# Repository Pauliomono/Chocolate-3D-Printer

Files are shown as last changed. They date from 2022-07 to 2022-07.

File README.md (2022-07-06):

# Chocolate-3D-Printer

3D printer that prints edible chocolate!
 
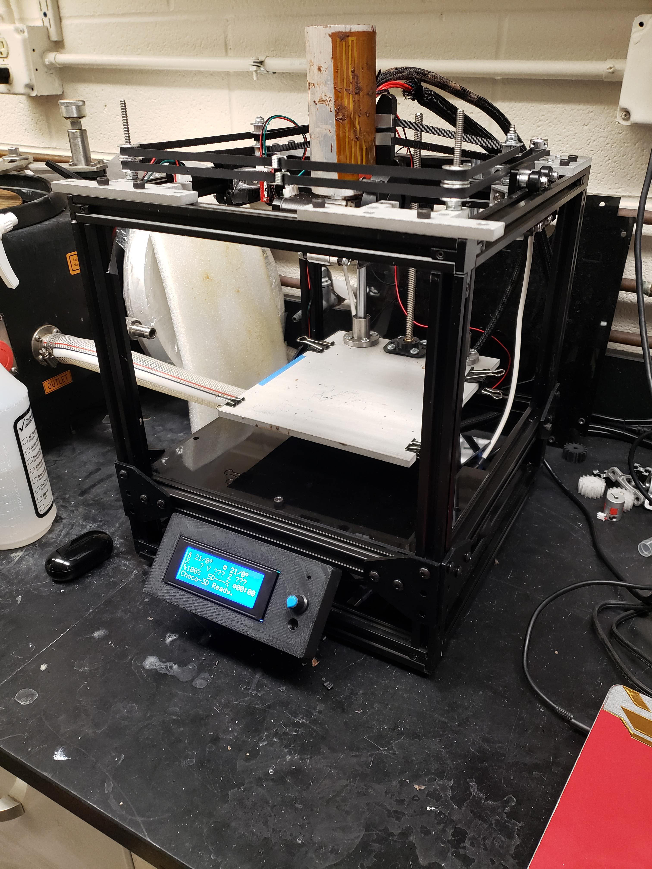
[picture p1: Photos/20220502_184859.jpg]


This 3D printer is capable of printing 3D objects from standard 3D printer .gcode files, such as the 3D Benchy demonstration print shown below.

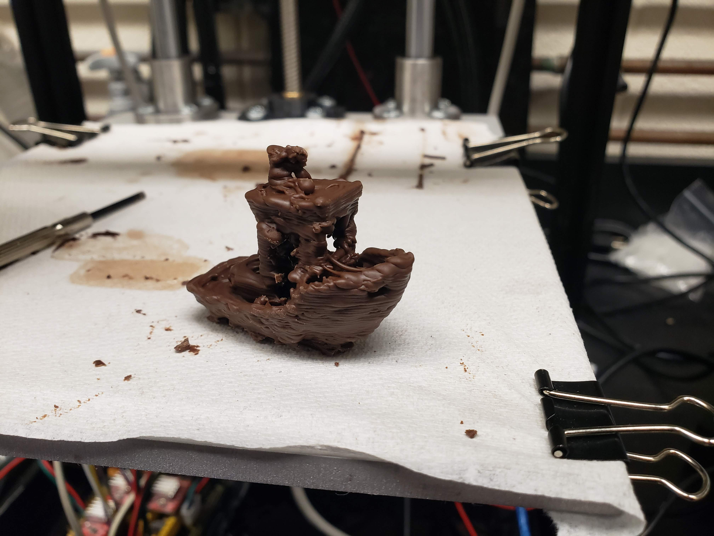
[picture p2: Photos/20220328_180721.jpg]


The Chocolate 3D Printer was designed in 2 iterations: the first as a group project during fall 2021 senior design and the second as an independent design project I worked on spring 2022.

For detailed information, the final report on this project is available under "Independent Design Project Final Report.pdf"

This project was created as a Mechanical Engineering Senior Design Project at the University of Notre Dame. Credit to Kassidy, Max, Morgan, and Thomas who were my teammates. The Chocolate 3D Printer is still equally yours as it is mine.

(printer in operation)



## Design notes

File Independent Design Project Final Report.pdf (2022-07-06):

Independent Design Project Spring 2022

Chocolate 3D Printer V2.0

Paul Mellor

May 3, 2022

Part 1: Original Project Overview

This project started as a Senior Design Project in the fall semester of 2021. The project was to

build a chocolate 3D printer (3DCP) that printed chocolate rather than plastic. It had the

following customer requirements: [1]

1. The 3DCP must print custom, detailed patterns and shapes out of chocolate.
2. The product must be safe to eat, durable, and taste good.
3. The 3DCP must create the pattern in a reasonable amount of time.
4. The 3DCP must be easy and safe to use.
5. The 3DCP should not require user intervention during the print.
6. The 3DCP must be easy to clean.
7. The 3DCP can be handled by up to two people and fit on the counter.
8. The 3DCP must be presentable and suitable for display.
9. The 3DCP can produce multiple copies during one print.
10. Power consumption is suitable for a standard household wall outlet.
11. The 3DCP must be affordable.

Based on the requirements we were given for Senior Design, a quantified list of design

specifications were created as the goals we intended to meet for the project. [1]

1. Through a combination of nozzle diameter, a recommended melting temperature of 31-36

°C, motor precision, and motion tolerance, the printer must be able to produce details as

small as 2 mm. The 3DCP nozzle diameter must not exceed 2 mm.

2. All parts of the 3DCP that come in contact with chocolate must be able to be washed and

be nontoxic in the 31-36 °C region. For example, any chocolate in contact with vinyl

tubing must not exceed 79.4 °C.

3. The volumetric flow rate should be at least 25 cm³
/hr.
4. All conductible materials near the heat source will have insulation or a cover and no

material will exceed 60 °C to avoid burns.

5. The 3DCP must store chocolate for the entire print: at least 100 cm³
of chocolate.
6. The parts must be able to come apart and fit together in order to clean easily. To remain

dishwasher safe, all materials must have a melting point above 180 °F.

7. OSHA standards specify that two people can comfortably carry 102 lbs. This 3DCP will

not exceed 51 lbs. The dimensions of the base will not exceed 2ft x 2ft

8. The 3DCP must have a viewing window that is at least 10 cm x 10 cm. All wires, motors

and electronics will be hidden.

9. The 3DCP must have a build area that is at least 10 cm x 10 cm.
10. The 3DCP must not use more than 1500 W of power.
11. The 3DCP fabrication must not exceed $1000 in purchased and manufactured parts.

These specifications drove the design choices we made for the original 3DCP.

Initial Design

The CAD model for the original design is shown below in Figure 1.

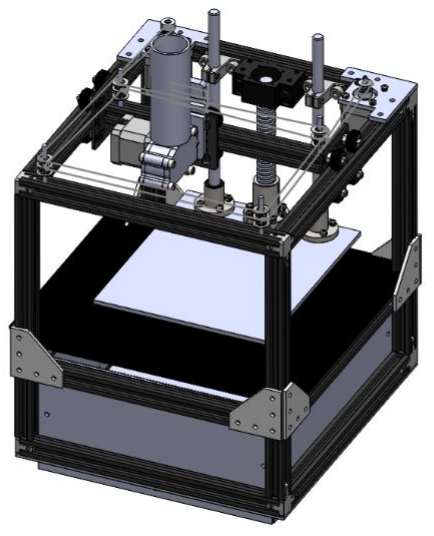
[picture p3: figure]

Figure 1: CAD model of the original 3DCP

To get a system that moved in 3 dimensions, the motion system moved the extruder in the x-y

plane while the build plate moved in the z direction. This was selected in order to minimize the

amount of power needed to quickly move the mass of the extruder body, vat, and chocolate

against the force of gravity. Starting with this principle, a CoreXY motion system was identified

which met the design specifications. Based on a specific arrangement of timing belts, it allows

the extruder to move anywhere in the x-y plane while the motors are fixed in place. A diagram of

this belt arrangement is shown in Figure 2.

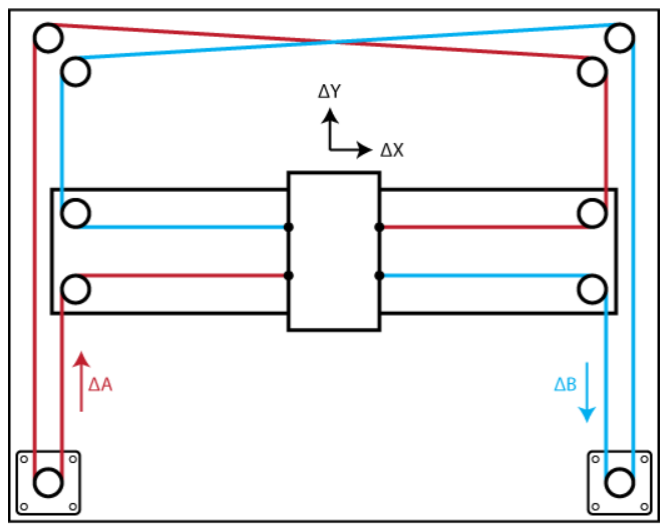
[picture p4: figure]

Figure 2: CoreXY diagram

The build plate was moved in the z direction using a combination of a lead screw and linear

guide rails. The gear reduction provided by the lead screw meant that a powerful motor wasn’t

necessary to hold the build plate against gravity. The guide rails kept the build plate stable and

took the bending loads of the bed.

The extruder design was modelled on a commercially available design called the

ChocoL3D extruder [2]. This was a gear-pump based design as opposed to the more common

syringe design. The gear pump extruder was chosen initially in order to minimize space taken by

a large syringe body and to improve the aesthetics of the design. It also allows better control for stopping and starting the extruder. Several iterations of the extruder were prototyped and tested

before the design was finalized and fabricated. The extruder design is shown below in Figure 3.

Electronics

The original design used an Arduino Mega as the microcontroller for the printer. It used a

“RAMPS 1.4 3D Printer Shield” that allowed it to interface with motors, heaters, and sensors.

The motors selected were stepper motors. They were simple to use with Arduino code, easy to

position with a high degree of precision, compatible with the RAMPS Shield, and powerful

enough to move the CoreXY motion system. 12V Electric heating elements were selected to heat

the gear pump and the vat for the extruder. Each also had a corresponding thermistor to provide

temperature feedback to the Arduino. A wiring diagram is shown in Figure 3.

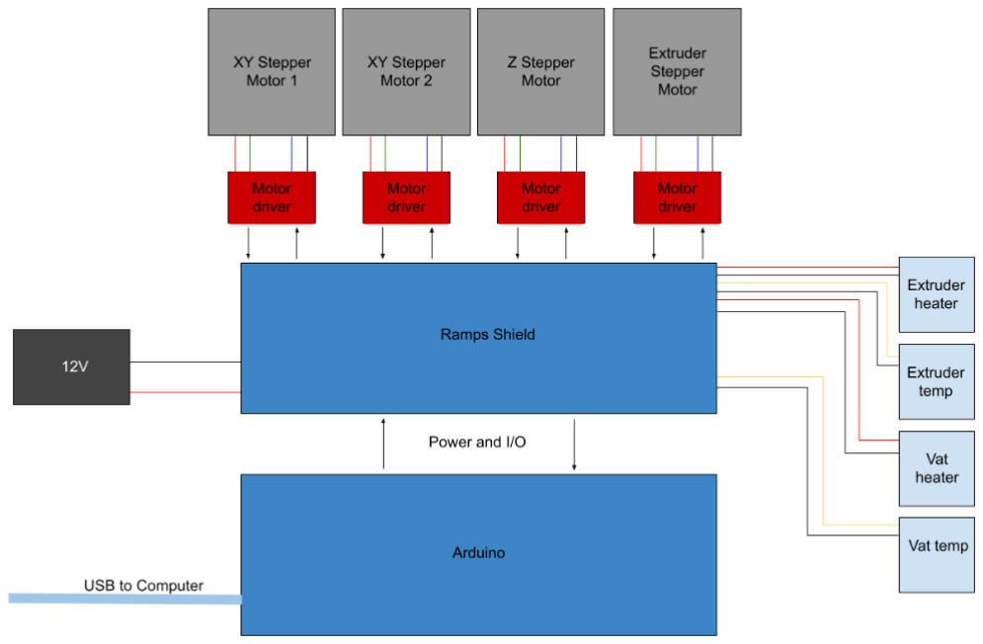
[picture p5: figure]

Figure 3: Wiring diagram of the Arduino

Software

In the original software system 3DCP began with a stereolithography (.STL) file for the

desired print object. The .STL file was imported into Cura, where it gets sliced and a G-Code file generated. The G-code file was converted into a .txt file and imported into MATLAB. A

MATLAB program parsed through the .txt file to interpret the G-Code and convert it to the

necessary coordinates to position the motors. The MATLAB program identified redundant layers

from the slicer to optimize storage space on the Arduino. The program outputted three matrices

of data points. The first two are the X and Y coordinates of the extruder. The third is a matrix full

of ones and zeros indicating if the extruder should be extruding during a given pass between

points.

These matrices were copied and pasted into the Arduino code and uploaded to the

Arduino board. The Arduino code then iterated through the matrices and performed the

necessary calculations for CoreXY to move the extruder carriage via two stepper motors. A third

stepper motor lowered the base plate between layers of chocolate. Once the Arduino code was

compiled, the board is connected to power to start the print. Figure 4 is a flowchart outlining the

sequence of the original software.

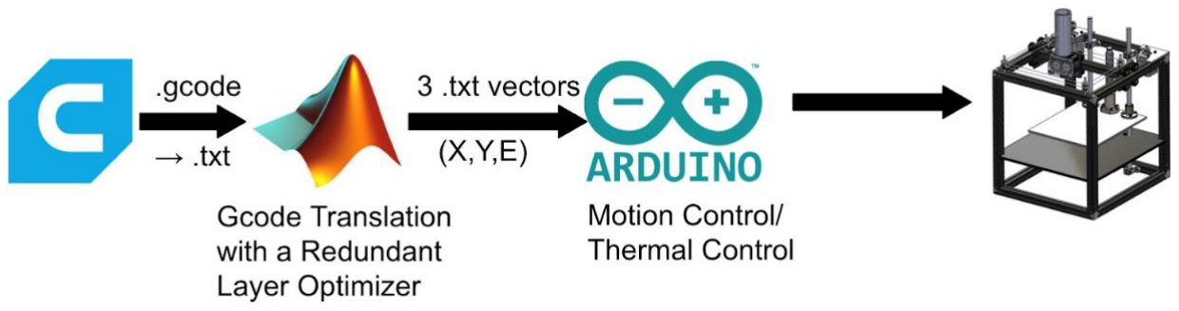
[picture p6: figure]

Figure 4: Flowchart of the Software System.

Results at the End of Senior Design

Figure 5 shows the 3DCP at the conclusion of Senior Design.

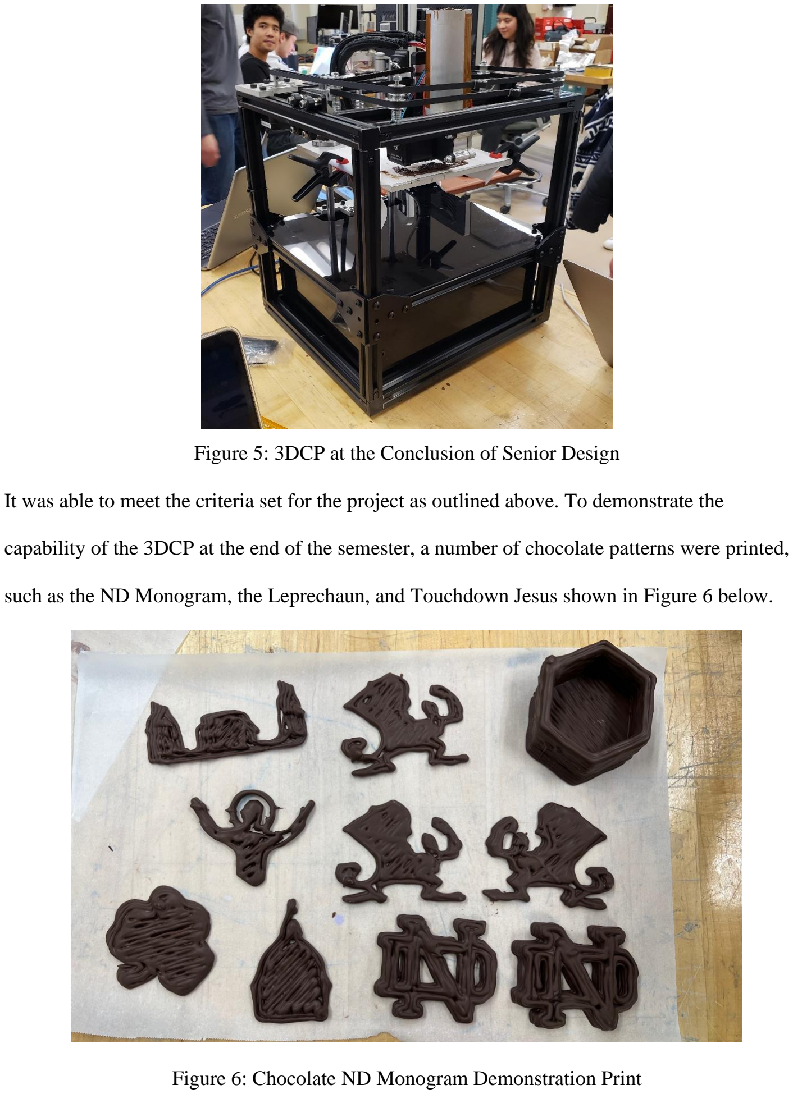
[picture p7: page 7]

Figure 5: 3DCP at the Conclusion of Senior Design

It was able to meet the criteria set for the project as outlined above. To demonstrate the

capability of the 3DCP at the end of the semester, a number of chocolate patterns were printed,

such as the ND Monogram, the Leprechaun, and Touchdown Jesus shown in Figure 6 below.

Figure 6: Chocolate ND Monogram Demonstration Print

Additionally, the 3DCP was capable of larger 3D prints, like the chocolate vase also pictured

above in Figure 6.

Problems

While this senior design project was successful, it was a good first iteration with

significant room for improvement. There were a number of issues that limited the printer’s

capability, and made it difficult to use. The first issue was the workflow required to go from 3D

model to completed 3D print. Using MATLAB to process the G-Code was confusing and

unintuitive. Reprogramming the Arduino for every new print was also a step that anyone without

programming experience would have a hard time completing, and made the 3DCP a rather

unadaptable system. This also had an unintended consequence – by making the coordinates for

the 3D print part of the code, the size of the print file was limited to the amount of flash memory

on the Arduino. In practice, this meant that any of our 3D prints had to contain less than ~800

distinct coordinates, severely limiting the complexity of geometry the 3DCP could print. This

effectively limited the 3DCP to printing a “thick 2D print” (printing the same pattern for every

layer).

- requirement of computer
- workflow to go from 3D model to actually printing
- limit to 2D shapes
- wait time between layers

Another problem with the 3DCP is that the chocolate took several minutes to solidify. This

meant that 1 layer could be printed reasonably quickly, but then the printer would have to wait

several minutes between layers before printing the next layer. The result was print times that

were sometimes double or triple in length to the time the printer spent actually moving.

- reliability (extruder working inconsistently, broken ball screw)

The last major problem the 3DCP had was reliability problems. First, extruder performance was

inconsistent. Sometimes it would produce consistent flow of chocolate, sometimes it would only

extrude chocolate in bursts, and sometimes it wouldn’t extrude any chocolate. Part of this had to

do with a finicky pre-heating procedure which involved reprogramming the Arduino with

separate code just to get everything up to temperature and flowing.

Part 2: The Second Iteration to Create Printer 2.0

With the foundation of the 3DCP from Senior Design, new goals were set to create a second

iteration of the 3DCP. These new additional goals were:

1. The 3DCP is able to print true 3D files. This includes more difficult structures like

overhangs and bridges.

2. The 3DCP can manage the heat of the printed chocolate such that it does not have to stop

printing in order for it to cool.

3. The 3DCP is user friendly enough that it can be operated by an average person who isn’t

necessarily experienced with 3D printing.

Software Changes

For the second iteration of the 3DCP the software was completely overhauled. The

Arduino was programmed with an open source piece of code called “Marlin”. Marlin is a

customizable piece of firmware specifically written for 3D printers. It is used on many

commercial 3D printers. It has a built-in G-code interpreter and can print directly using a G-code

file. It handles all of the kinematics of the motor, with built-in configurations for CoreXY motion

systems. It handles the heaters using sophisticated PID controllers. It has built-in functionality for adding a user interface. Finally, it designed to use an SD card (or some external storage

media) for storing G-code files.

Switching to Marlin has significant advantages over the original code written for the

3DCP. First, it greatly simplified the workflow going from a 3D file to a printed 3D object.

Instead of slicing in Cura, parsing in MATLAB, and reprogramming the Arduino, the sliced file

straight from Cura only needs to be placed on an SD card and connected to the controller.

Someone with little to none programming experience can translate a 3D file into something the

3DCP can print with Marlin. Second, the use of an SD card effectively removes the limitation on

the number of coordinates for the 3D print. Even highly detailed 3D models don’t come close to

the gigabytes level capacities of an SD card. Finally, if G-code files are left on the SD card, the

3DCP can be operated without any access to a computer whatsoever.

Cooling System

For the second iteration of the 3DCP, a cooling system was added to the printer. To

decrease the time needed to print, the extruded chocolate needed to solidify as quickly as

possible. Two approaches were considered to solve this issue: either cool the chocolate using

conduction through the build plate, or cool the chocolate using forced convection from a fan.

Conduction was ultimately decided against. While chilling the build plate would likely be very

effective at cooling the first few printed layers, the more layers that were built up, the less

effective conductive cooling would be. Since convection could provide consistent cooling

performance regardless of the number of layers in the print, a study was done to see if forced

convection from a fan could effectively cool the chocolate more quickly.

To find the feasibility of using convective cooling to help solidify the chocolate, a

cooling calculation was done to simulate how effectively convection could cool a layer of chocolate. A 20mm x 20mm x 1.5mm box was used to represent the shape of a single chocolate

layer. Using the lumped capacitance method, the temperature T of the chocolate as a function of

time is given by:

T(t) = T∞ + (T0 − T∞)e

−

t
τ

where T∞ is the ambient temperature, T0 is the initial temperature, and τ is the time constant. τ is

equal to

τ =

cpρV
ℎA

where cp is specific heat (1006 J/kg-K) [4] , ρ is density (1.225 kg/m^3) [4], V is volume, ℎ is

the convection coefficient, and A is surface area. ℎ for forced convection from a fan was taken to

be a conservative 60 W/m^2-K [4]. A plot comparing the forced convection from a fan to natural

convection is shown in figure 7.

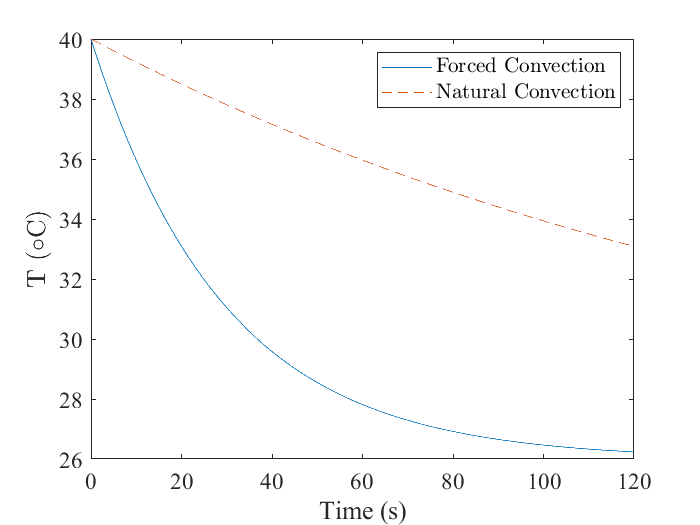
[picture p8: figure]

Figure 7: Theoretical Convective Cooling for Chocolate

This demonstrated that adding a fan would make a significant difference in cooling the

chocolate quickly. Based on Figure 7, cooling the chocolate from the print temperature of 40 ℃

to below to melting point of 32 ℃ only took 25 seconds – significantly less than the 3+ minutes

required between layers at the end of senior design. Based on this proof of concept, a cooling fan

was added to the extruder, shown in figure 8 below.

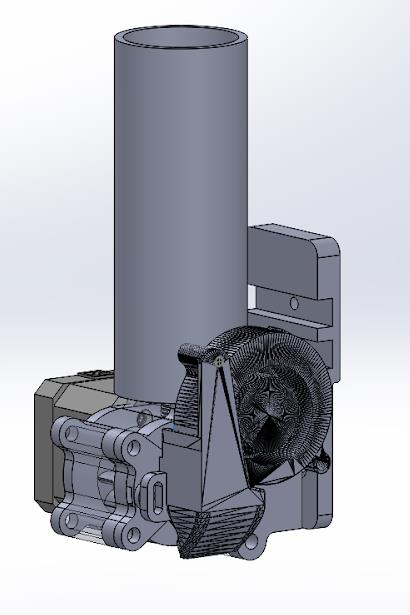
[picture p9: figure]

Figure 8: Cooling System on the Extruder

User Interface

For the second iteration of the 3DCP, a user interface was added. A small display and a

control knob were added to the front of the 3DCP. The screen can be used to show useful

information about the printer, show menus for controlling and configuring the printer, and

initiate 3D prints. The control knob can be used to navigate these menus and select items. In

conjunction with Marlin as the firmware, a whole host of useful functionality is now readily available to anyone using the printer. Examples of the home screen and available menus are

shown in Figures 9 and 10 below.

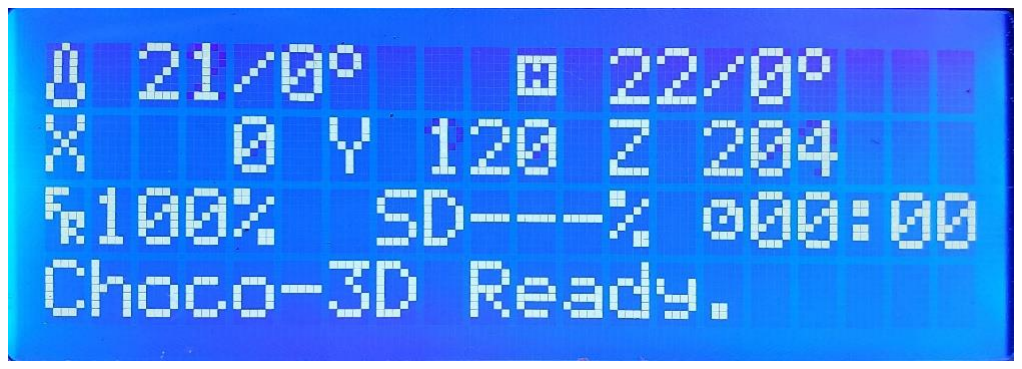
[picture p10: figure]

Figure 9: Home Screen

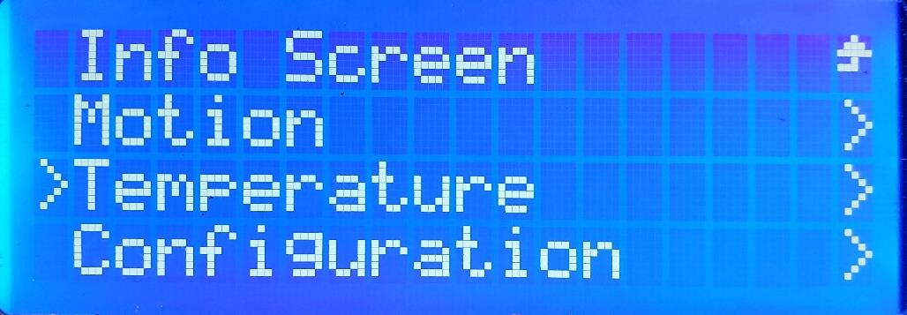
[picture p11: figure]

Figure 10: Menus on the 3D printer

Documentation & Resources

In addition to adding a user interface, a whole host of documentation and resources were

created to make the 3DCP accessible and usable by inexperienced persons. First, the SD card on

the 3D printer is loaded with multiple premade print files. A user can simply plug the printer in,

select one of these files, and the printer automatically starts. No experience with a 3D printer

slicer is required.

If a user wants to print their own 3D model, a slicing profile was created for CURA

Slicer. Uploading this profile automatically changes the slicer parameters (layer thicknesses, line

widths, flow rates, temperatures, retraction settings, supports, etc) to specifically work with the

3DCP. This allows someone without much experience with 3D printing slicers to still print their

own custom 3D models.

Finally, the biggest resource created for the 3DCP was a user guide. This guide gives

step-by-step instructions for turning on and warming up the printer, generating the G-code files

for 3D prints, and starting a 3D print. It also includes a troubleshooting guide to help fix

common issues that might occur with the 3DCP. This document is attached in the Appendix.

Results

Figure 11 shows the 3DCP at the conclusion of the spring semester.

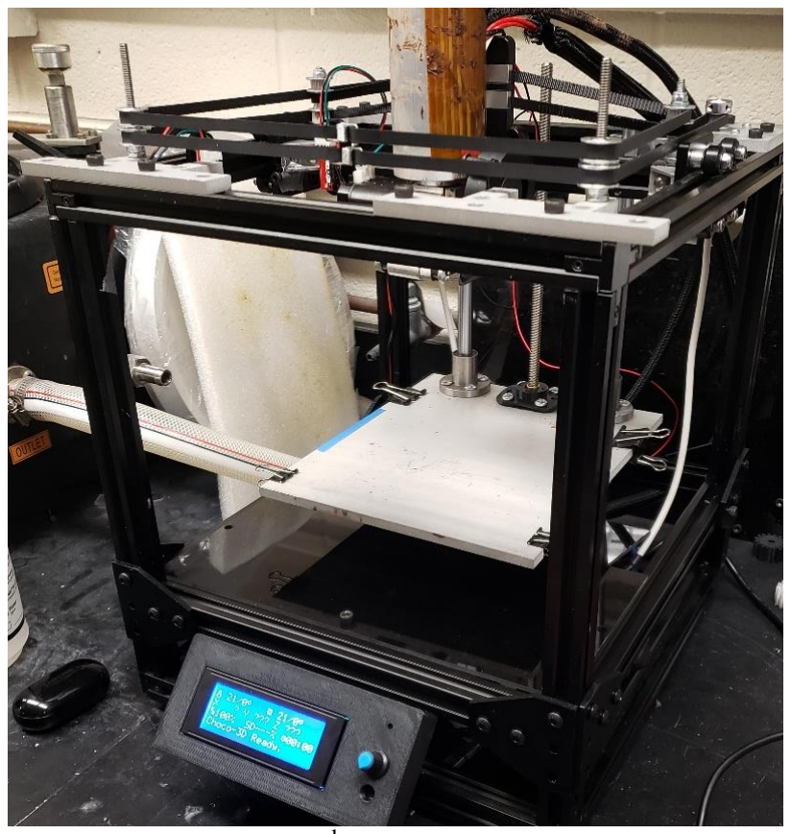
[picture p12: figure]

Figure 11: 2nd Iteration of the 3DCP

Most of the printer remains unchanged from the first iteration, but its capabilities have vastly

improved in terms of printer performance and usability. The 3DCP is now able to print true 3D

models with complex geometry. An example of what it is now capable of printing is shown in

Figure 12.

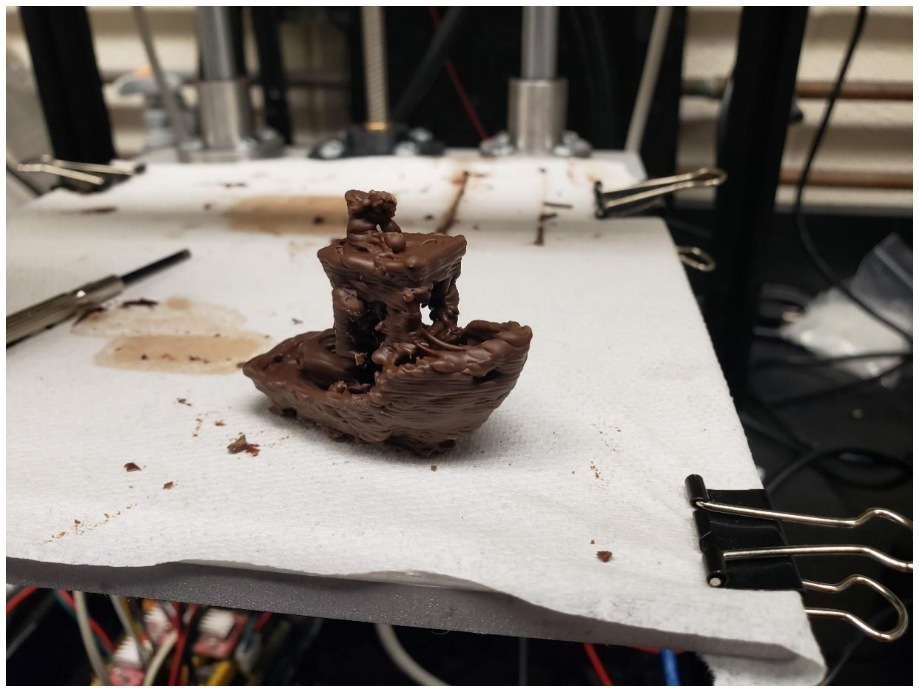
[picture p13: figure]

Figure 12: Example of Chocolate 3D Print Compared to the 3D Model

This print has overhangs, bridges, complex details, and was printed in only 30 minutes. The

finished print is dimensionally within ±1mm of the original 3D model. Finally, the 3DCP was

able to cool the chocolate well enough that it only had to pause between layers for the uppermost

layers of the smokestack that only took a few seconds each to print.

To evaluate the user friendliness of the 3DCP, several people unfamiliar with the 3DCP

were given the user documentation and resources and shown the 3DCP. They were then asked

print the model shown in Figure 12 (The print file was premade and already loaded on the SD

Card in the 3DCP). All of them were able to successfully start the print with the use of the

provided resources. One person was even able to start the 3D print without consulting the

documentation whatsoever, and commented that the menus on the printer were surprisingly

intuitive to follow.

Remaining Areas for Improvement

This second iteration of the 3DCP represented a huge step forward for the 3DCP, but

there are still remaining areas where the 3DCP could improve. First, the 3DCP still only works

with one kind of chocolate. More time could be spent testing with different chocolate types and

tuning the printer to work with different materials. This would make the printer more

flexible/adaptable instead of locking it to exclusively the chocolate it prints with now.

Secondly, the 3DCP does not print with a consistent line width, especially at slow speeds.

This is likely due to the gear pump design for the extruder not producing consistent pressure at

low speeds. A combination of redesigning the geometry of the gear pump and increasing the

print speed could either mitigate this issue or fix it altogether.

Third, the gear pump design does not work well with smaller nozzle sizes. For nozzles

smaller than 1mm in diameter, the extruder tends to jam and does not extrude at all. Redesigning

the gear pump may fix this problem, but this may also be a limitation of the gear pump concept

for the extruder.

Finally, the 3DCP lacks some features that are common “nice to have” features often

found on many normal 3D printers. It does not have a bed levelling mechanism, quiet motors, a

camera to watch/record the printing process, or internet connectivity. While not strictly necessary

to the operation of the 3DCP, these are features that would make the 3DCP a more well rounded

product.

Appendix A: References

[1] Senior Design Design Proposal, Group 5, Notre Dame AME Senior Design Fall 2021
[2] ChocoL3D, L3D Extruder’s Body. https://chocol3d.com/product/l3d-extruder-kit/
[3] Convection Heat Transfer Coefficients, Philip Kosky,

https://www.sciencedirect.com/topics/engineering/convection-heat-transfer-coefficient

[4] Air Specific Heat Capacity, Engineering Toolbox, https://www.engineeringtoolbox.com/air-

specific-heat-capacity-d_705.html (https://www.engineeringtoolbox.com/air-specific-heat-capacity-d_705.html)

Appendix B: User Guide

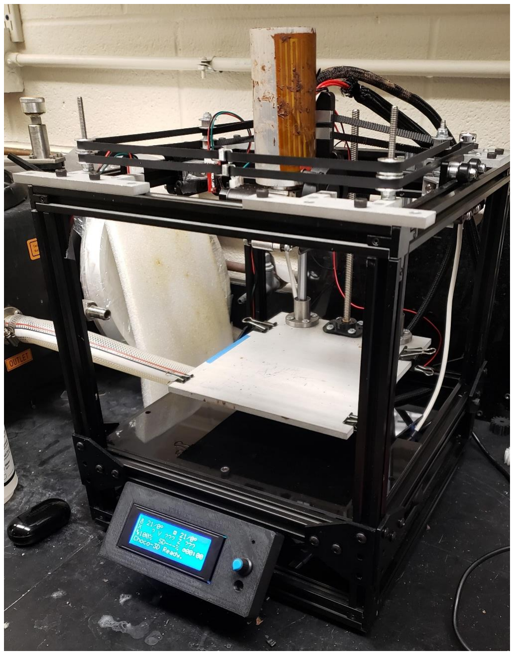
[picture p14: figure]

# The 3D Chocolate Printer

# (3DCP)

# User Guide

Overview

This is the home info screen for the 3DCP.

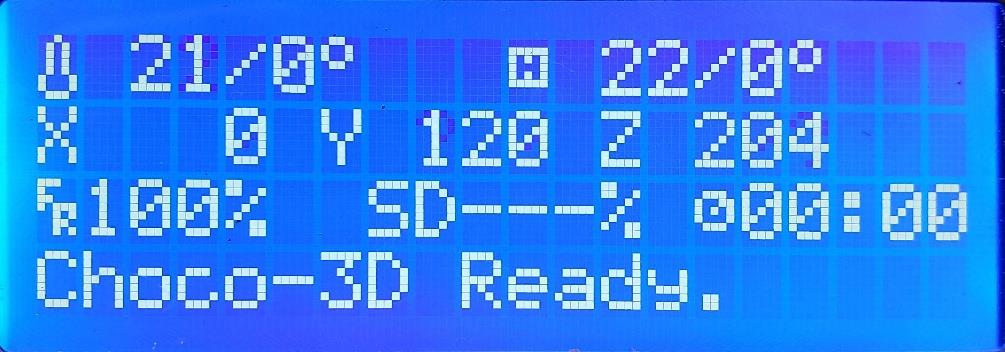
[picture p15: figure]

It gives a host of information about the printer.

- The top row shows the temperature of the of the Chocolate Vat and the Extruder.
- The 2nd row shows the position of the printer in millimeters.
- This may be inaccurate until the printer has been homed (The 3DCP will home itself automatically at the beginning of every print)
- The 3rd row tracks the progress of a 3D print, showing both % completed and time elapsed.
- The bottom row displays any relevant messages or errors the 3DCP might have.

To the right of the screen is the control knob.

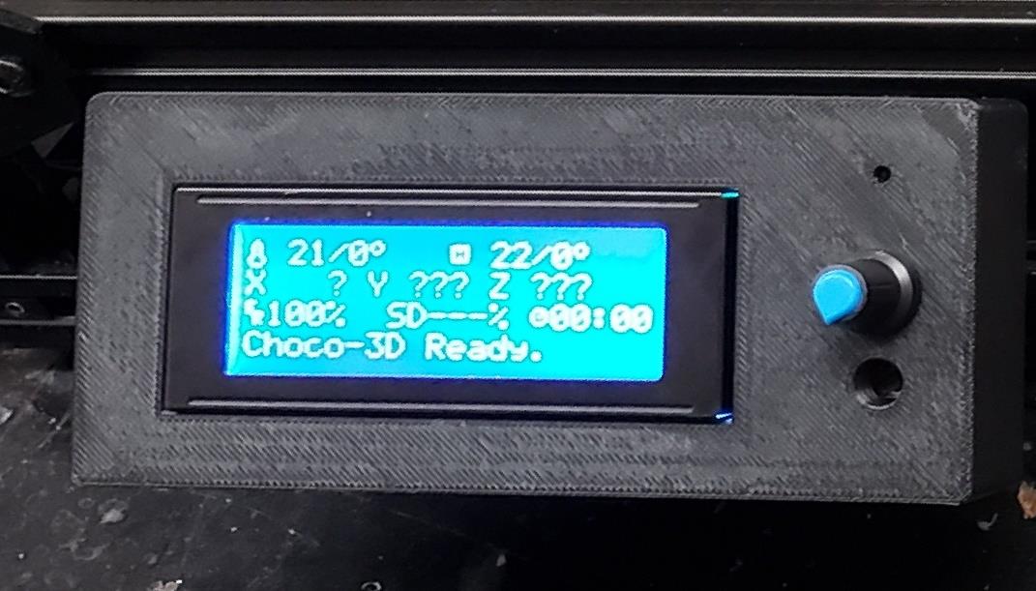
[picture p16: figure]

Twisting this knob allows the user to scroll through menus. Pressing the knob allows the user to select something.

On the left side of the screen is the SD card slot. This is where print files are stored, and this is how print files are moved from a computer to the 3DCP.

Preheating Procedure

Before starting any prints, the 3DCP must be preheated. This procedure melts the chocolate so that it is able to be printed. DO NOT START A PRINT UNTIL THE PREHEATING PROCEDURE IS COMPLETE.

1. To start the preheat, open the main menu and select “Temperature”:
2. Select “Preheat Choco”:

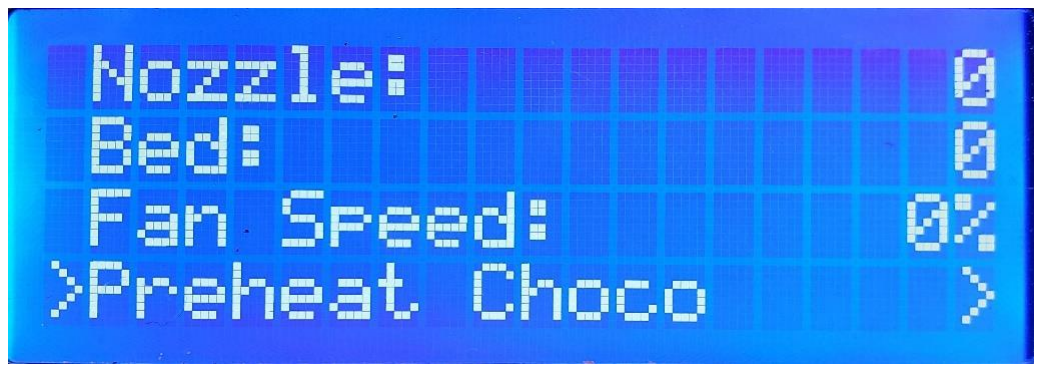
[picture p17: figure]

3. Select “Preheat Choco”:

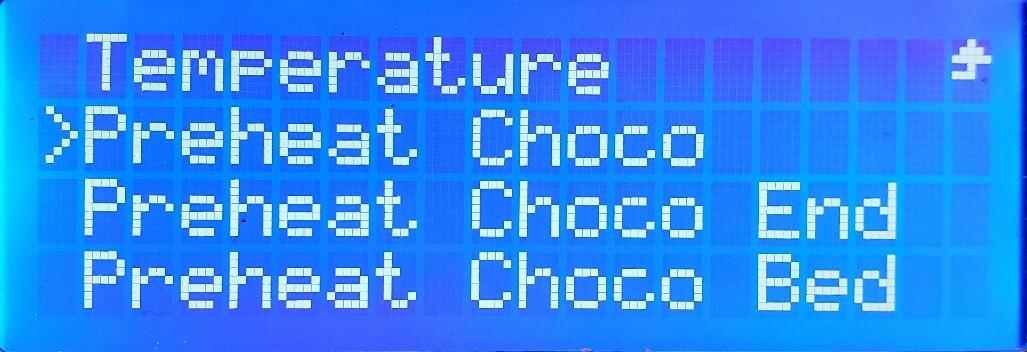
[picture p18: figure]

4. Once this is completed, return to the home screen.
5. WAIT. This step may take 10-15 minutes. Periodically check the chocolate in the vat. When the Chocolate in the vat is melted, the Preheating Procedure is complete. The 3DCP is now ready to print.

Start a 3D Print

Ensure that the preheating procedure has been completed before starting a print. The 3DCP will not print properly until the chocolate is warmed up and melted.

1. To start a 3D print, open the main menu and scroll down to select “Print from Media”:

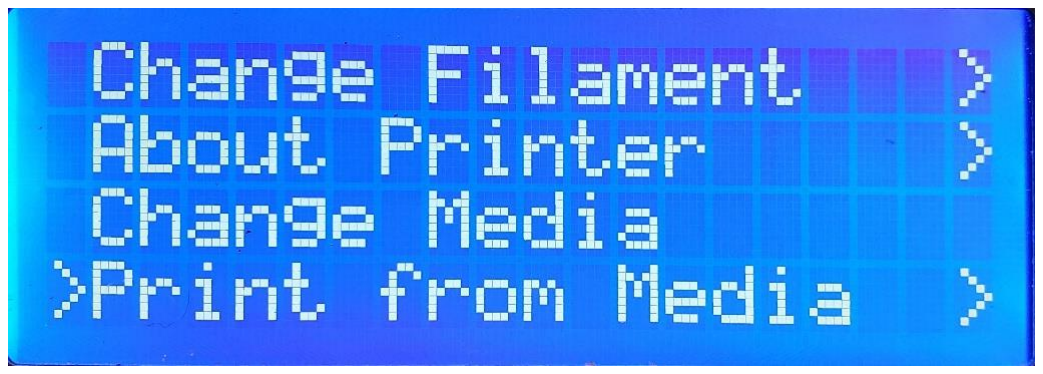
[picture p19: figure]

2. Select the model to print. In this example, “CE3_3DBenchy.gcode” will be printed.

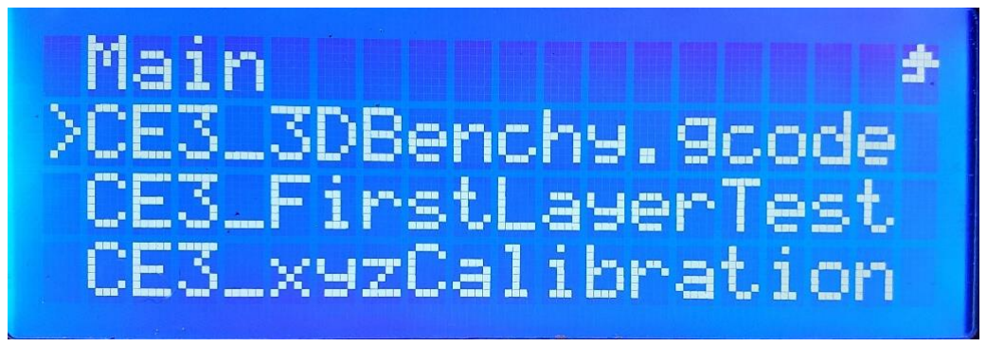
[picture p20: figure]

3. Select “Print” and the 3DCP will start the print.

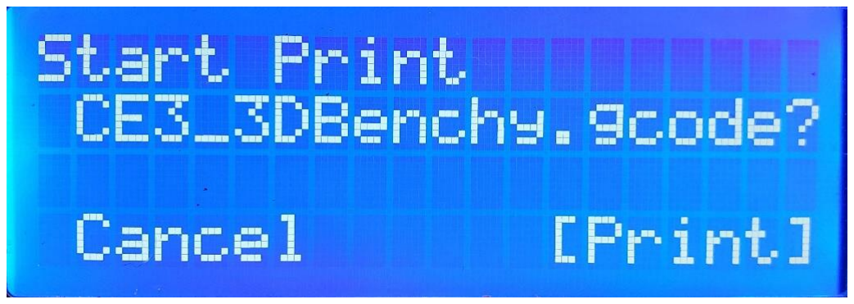
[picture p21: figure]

Using CURA to Slice 3D files

CURA is a 3D slicer that can be used to generate G-code files for the 3DCP to print. This procedure outlines setting up the 3DCP in CURA and adding a profile for printing chocolate.

1. Open CURA.
2. In the top left corner, click on “settings => printer => add printer”. The following menu will appear.

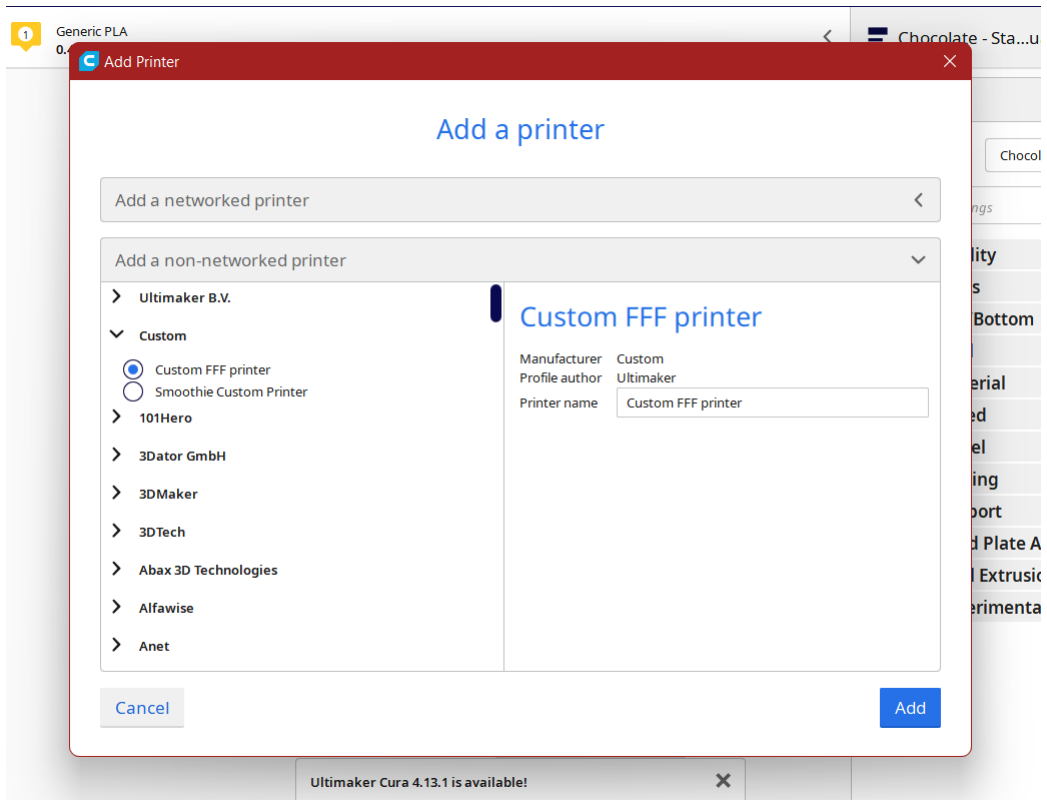
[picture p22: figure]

3. Click the “Add a non-networked printer”, select “Custom” and “Custom FFF Printer”.
4. Give it a name in the “Printer name” box on the right, and hit “Add”. The Machine Settings should now appear.

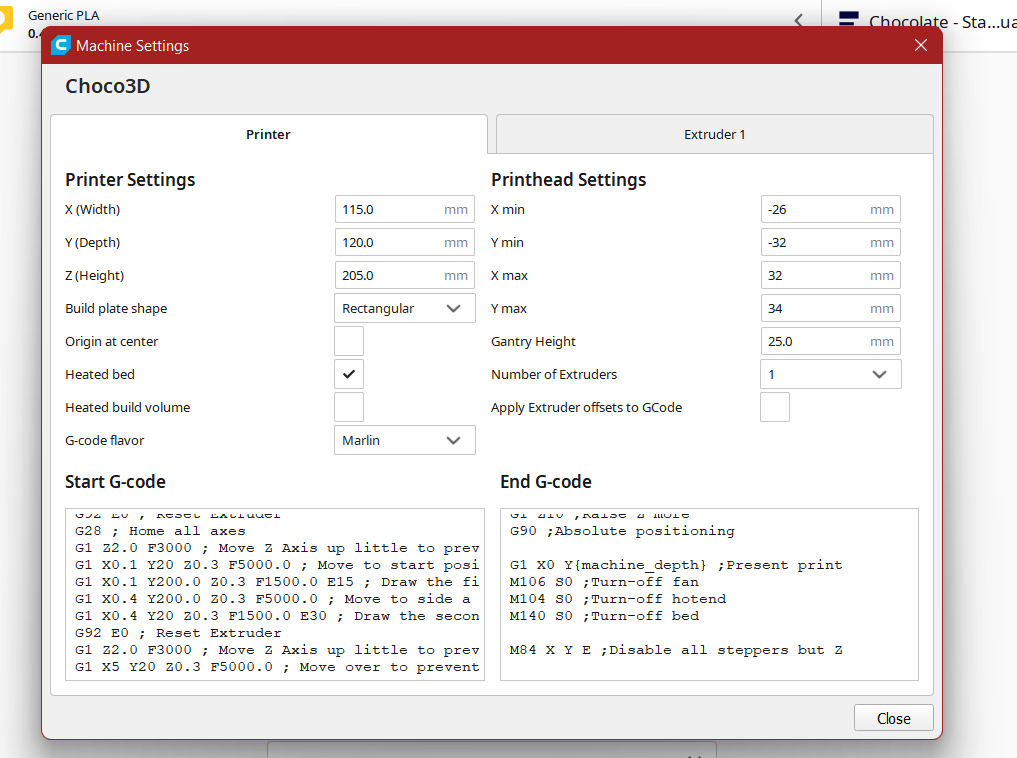
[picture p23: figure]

1. Change the “X (Width)” value, the “Y (Depth)” value, and the “Z (Height)” value to match those shown above.
2. Select Build plate shape to be “Rectangular”.
3. Make sure “Heated Bed” is checked.
4. Select “Marlin” as the G-code flavor.
5. Make sure “Apply Extruder offsets to Gcode” is NOT checked.
6. Paste the following in the “Start G-code” box:

G92 E0 ; Reset Extruder
G28 ; Home all axes
G1 Z2.0 F3000 ; Move Z Axis up little to prevent scratching of Heat Bed G1 X0.1 Y20 Z0.3 F5000.0 ; Move to start position
G1 X0.1 Y200.0 Z0.3 F1500.0 E15 ; Draw the first line
G1 X0.4 Y200.0 Z0.3 F5000.0 ; Move to side a little
G1 X0.4 Y20 Z0.3 F1500.0 E30 ; Draw the second line
G92 E0 ; Reset Extruder
G1 Z2.0 F3000 ; Move Z Axis up little to prevent scratching of Heat Bed G1 X5 Y20 Z0.3 F5000.0 ; Move over to prevent blob squish
7. Paste the following in the “End G-code” box:

91 ;Relative positioning
G1 E-2 F2700 ;Retract a bit
G1 E-2 Z0.2 F2400 ;Retract and raise Z

G1 X5 Y5 F3000 ;Wipe out
G1 Z10 ;Raise Z more
G90 ;Absolute positioning

G1 X0 Y{machine_depth} ;Present print M106 S0 ;Turn-off fan
M104 S0 ;Turn-off hotend
M140 S0 ;Turn-off bed

M84 X Y E ;Disable all steppers but Z

8. Select “close” in the bottom right to exit the settings.

The 3DCP is now set up in CURA. To add a profile to print chocolate, use the following steps.

9. Click the “Print Settings” drop-down in the top right. Click the dropdown next to “Profile” and select “Manage Profiles”.

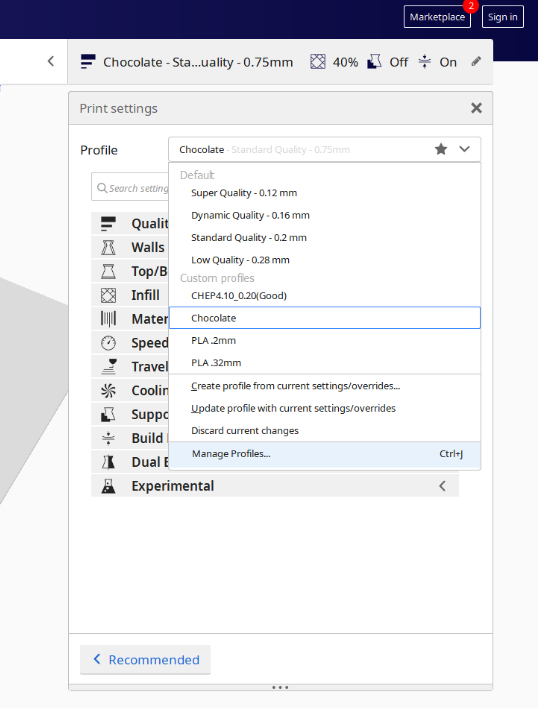
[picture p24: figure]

10. In the Profiles menu, select the “Import” button.

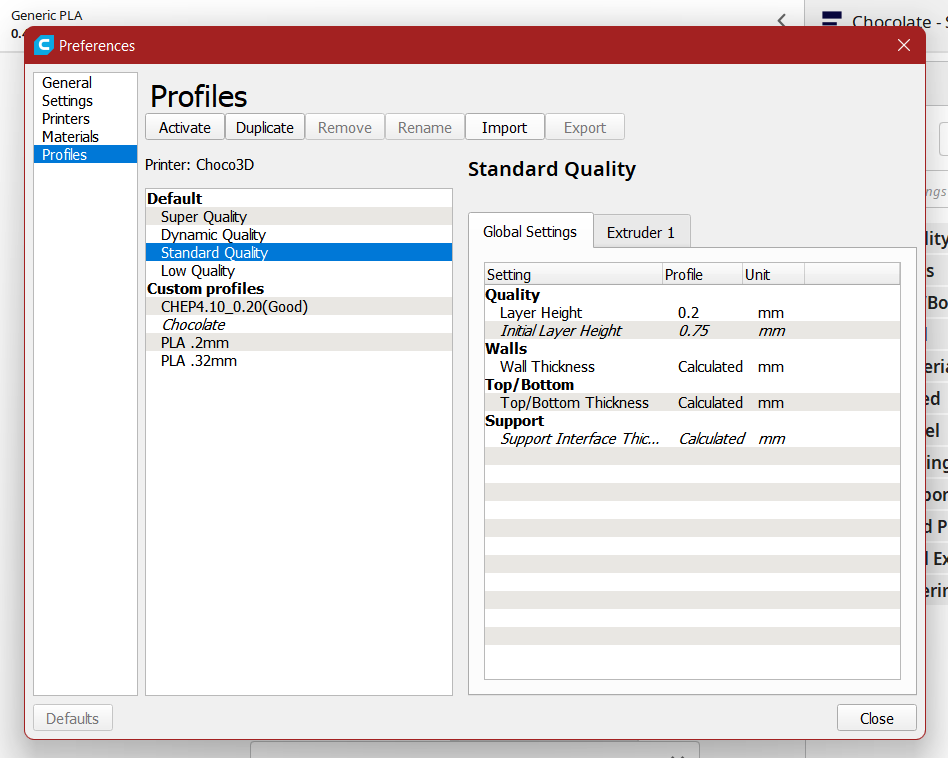
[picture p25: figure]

11. Use the file “Chocolate_Cura_Profile.curaprofile”. It should appear under the Custom profiles tab.
12. Select the profile and hit “Activate” at the top left.
13. Close the menu.

CURA is now properly configured for the 3DCP. Upload any .STL file and CURA will generate a G-code for the 3DCP. Save the .gcode file to the SD card and insert the SD card into the 3DCP to print it.

Wiring Diagram

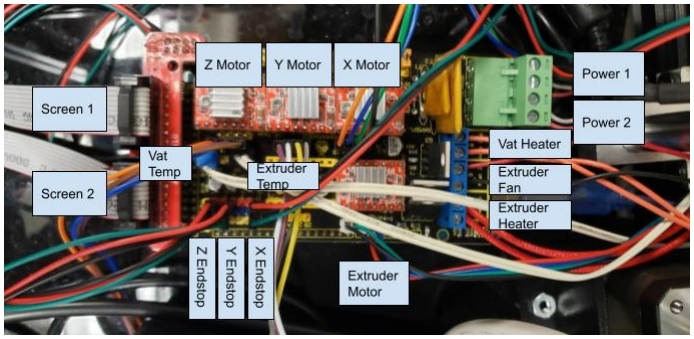
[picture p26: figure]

Additional wiring info can be found on the controller’s website here:

https://reprap.org/wiki/RAMPS_1.4

Troubleshooting Common Problems

### 1. Print from Media doesn’t appear in menu:

a. Remove and re-insert the SD card. Sometimes it doesn’t seat correctly in the SD card slot.
b. Verify that the SD card appears if plugged into a computer. If not, there may be an issue with the SD card

### 2. Extruder/Vat is “Heating” but the indicated temperature is not changing:

a. Check that the thermistor (sensor with white wires) is inserted into the extruder
b. Check that the thermistor (sensor with white wires) is plugged into the controller correctly (see wiring diagram)
c. Check the heater wires are wired correctly (see wiring diagram)
d. Note – the 3DCP does have a feature called “Thermal Runaway Protection”. While heating, if it does not detect a change in temperature for the vat/extruder after a certain period of time, it will throw an error and cease heating. Occasionally, the vat heats slowly enough that it triggers this protection. Unplug and re-plug in the 3DCP to reset it.

### 3. The print has started, but chocolate isn’t coming out of the extruder:

a. Verify that the chocolate is completely melted. Perform the preheating procedure again.
b. Listen to the extruder motor. If it is making a clicking sound, it is skipping and not extruding correctly.
i. Loosen the 4 bolts on the cover of the extruder slightly.
c. Poke a needle up the nozzle to verify that the nozzle is not clogged. If the needle is covered in melted chocolate, the nozzle is not clogged.
d. Use the temperature menu to increase the extruder temperature by a few degrees

### 4. The print has started, but only a small amount of chocolate is coming out of the

extruder:
a. Add more chocolate to the vat. When the vat gets low, the extruder does not extrude well.
b. In the “tune” menu while printing, increase the “flow rate” parameter.

### 5. The Motors are very loud:

a. Are they moving? Yes:
i. This is probably normal: these stepper motors can be very noisy under load, especially the Z axis motor
ii. Remove anything loose in the bottom of the 3DCP (bolts, screws, etc.) that could be vibrating
b. Are they moving? No:
i. Check to see if any of the motion system caught.
ii. Try homing the printer: under the “motion menu” select “Auto Home”.

Appendix C: Final Budget

Note: A Screen and Limit switches were provided by Mr. Brownell and are not included in the final budget.

Item | Cost
T8 Lead Screw | $10.99
MicroSD Card | $9.49
12V Fans | $10.79
Chocolate | $6.79
Acrylic Panels | $17.99
Total | $56.05

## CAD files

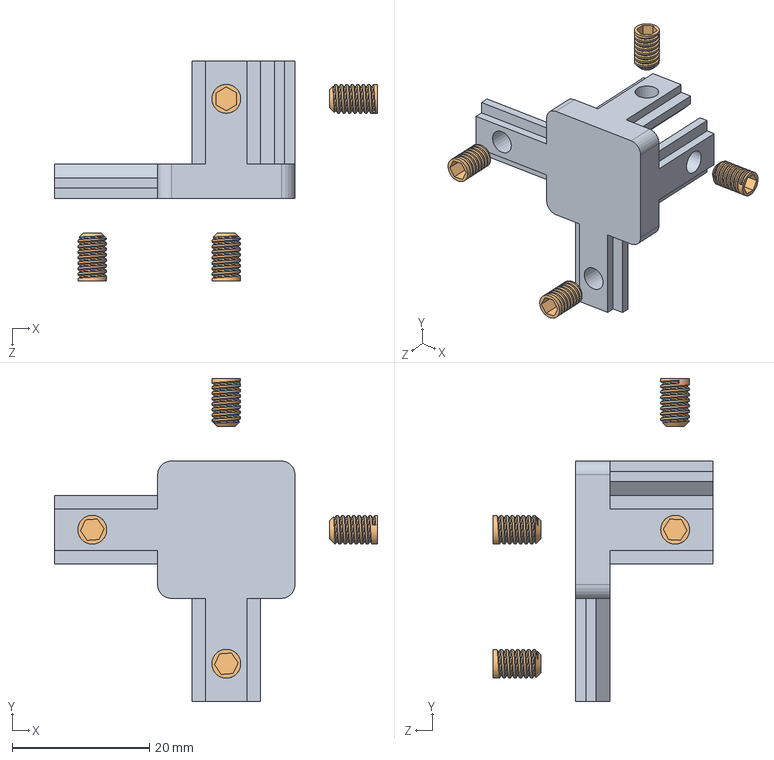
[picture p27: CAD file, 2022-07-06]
CAD Model/Corner_Bracket_SubAssembly.SLDASM
47.0 x 47.0 x 32.0 mm
2020 3-way corner bracket (v2)
Bracket_Screw x 4

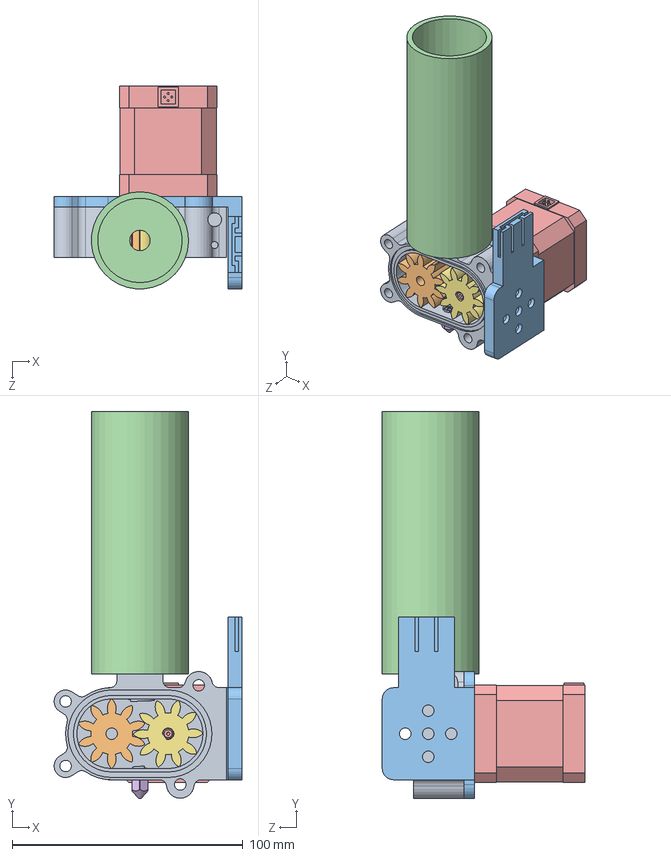
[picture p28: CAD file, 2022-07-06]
CAD Model/New Gear Pump/NewGearPumpAssembly.SLDASM
81.5 x 167.9 x 88.1 mm
body_newgearpump
Gear_newgearpump
Extruder_mount
vat_newgearpump
DC_Steppers
3695N115_3D Printer Nozzle
Gear_key_newgearpump

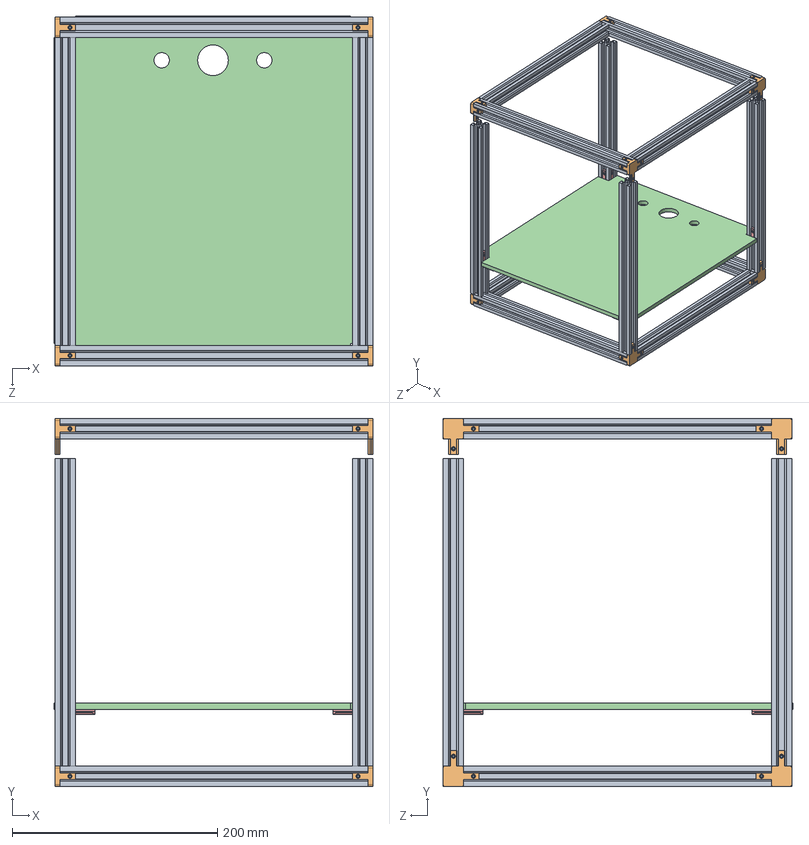
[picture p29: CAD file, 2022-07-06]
CAD Model/Frame.SLDASM
311.0 x 358.9 x 341.0 mm
V-slot-aluminum x 12
2020 3-way corner bracket x 8
92605A657_Stainless Steel Flat-Tip Set Screw x 40
bottom_cover_plate
Forseti-CTI20-01 - Cantoneira interna base 20 v-slot x 8

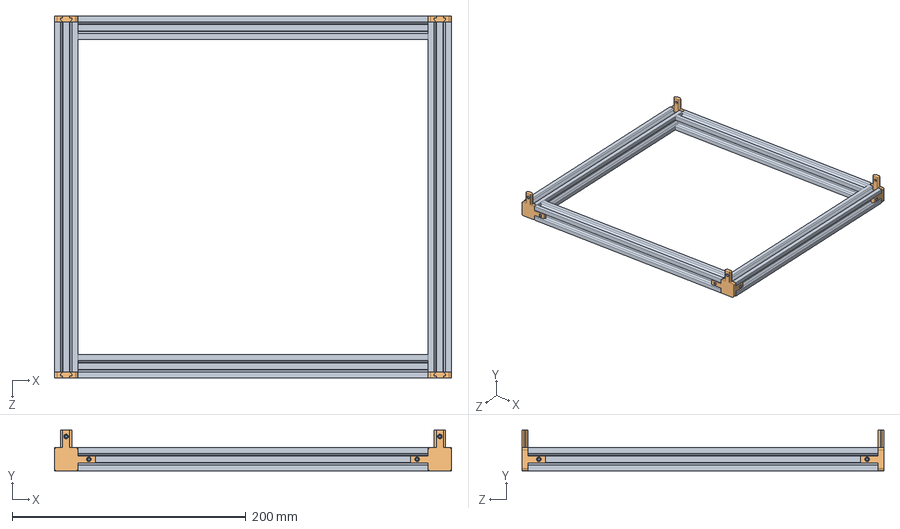
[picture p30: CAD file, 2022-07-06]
CAD Model/Base.SLDASM
340.0 x 35.0 x 310.0 mm
V-slot-aluminum x 4
2020 3-way corner bracket x 4
92605A657_Stainless Steel Flat-Tip Set Screw x 16

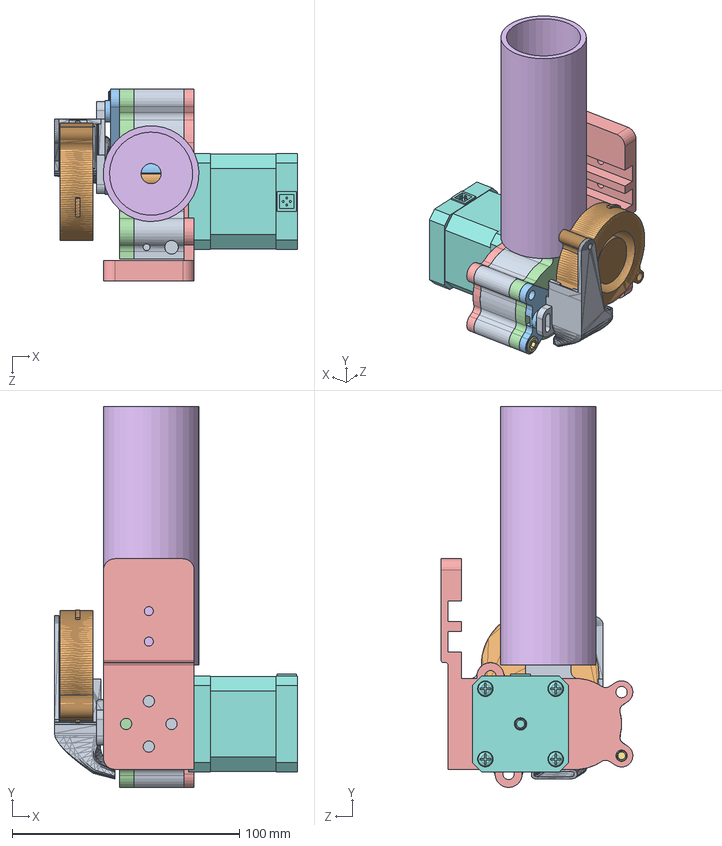
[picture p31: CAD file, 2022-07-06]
CAD Model/Extruder_Assembly.SLDASM
107.1 x 167.8 x 84.5 mm
body_newgearpump
Gear_key_newgearpump
Gear_newgearpump
cover_newgearpump
Extruder_mount_IDEA2
vat_newgearpump
DC_Steppers
5015_Lightweight_Duct_Standard_Left
fan_5015-blower
fan_mount

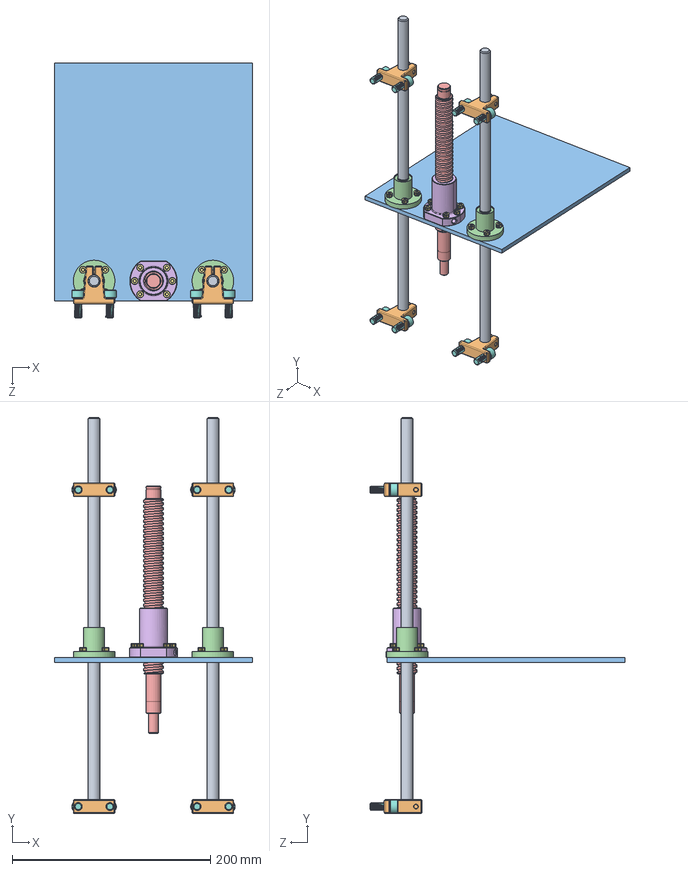
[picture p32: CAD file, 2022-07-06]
CAD Model/Z_Axis_motion.SLDASM
200.0 x 400.0 x 257.2 mm
6112K104_Linear Motion Shaft x 2
61815K34_Base-Mounted Shaft Support x 4
BuildPlate
Linear Bearing x 2
Generic Ballscrew
SFU-1605.step
91290A144_Black-Oxide Alloy Steel Socket Head Screw x 14
96144A211_Fine-Thread Alloy Steel Socket Head Screw x 8

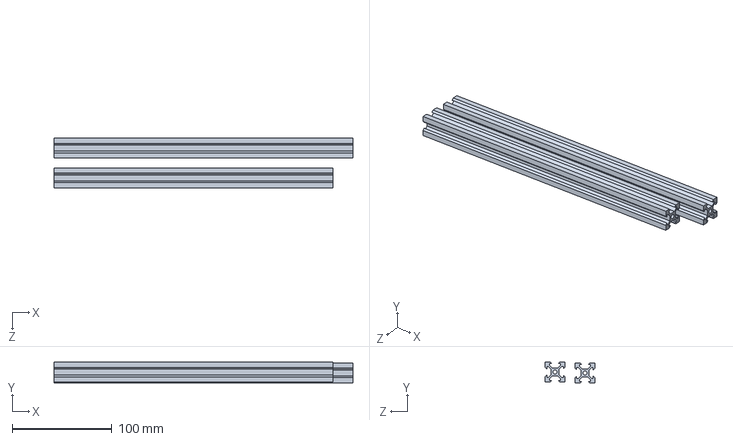
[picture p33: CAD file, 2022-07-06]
CAD Model/Extrusion_for_drawing.SLDASM
300.0 x 20.9 x 50.0 mm
V-slot-aluminum x 2

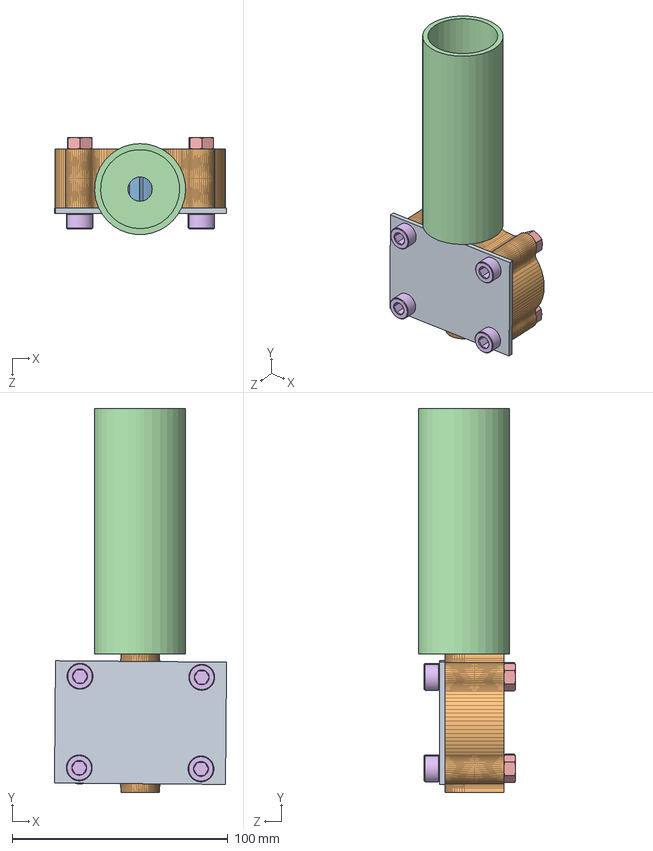
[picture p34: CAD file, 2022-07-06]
CAD Model/GearAssem.SLDASM
79.7 x 177.9 x 45.1 mm
extruder_cover_piece
gear_again_lol
gear_tight_fixed x 2
simple_vat
90592A018_Steel Hex Nut x 4
91290A162_Black-Oxide Alloy Steel Socket Head Screw x 4

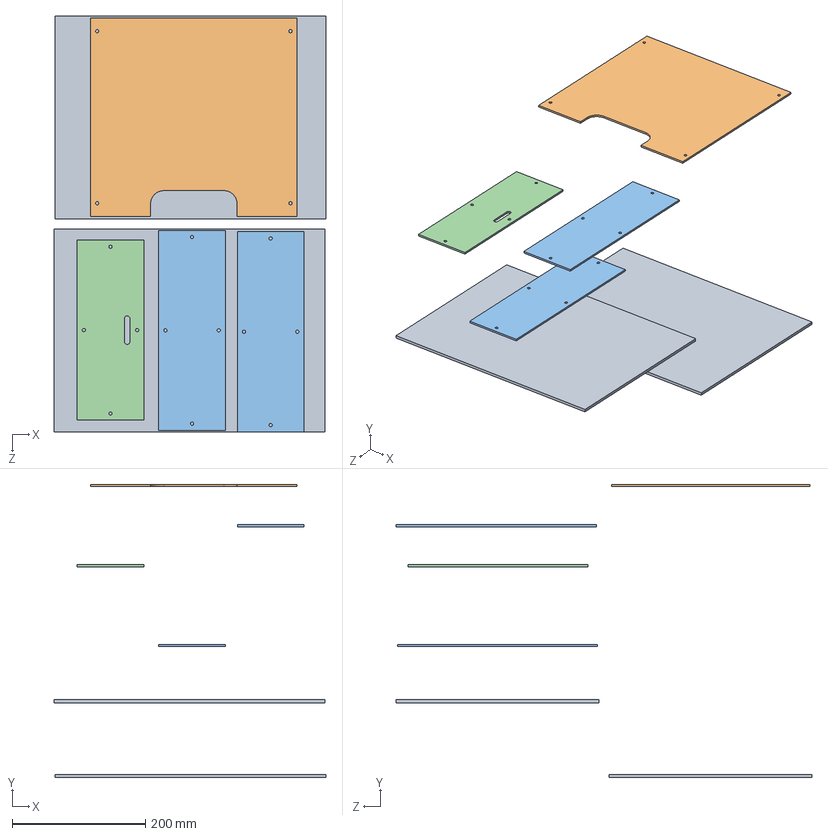
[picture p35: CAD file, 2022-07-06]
CAD Model/panels_waterjet.SLDASM
407.3 x 440.0 x 623.9 mm
stock x 2
bottom_cover_plate
Side_Plate_1 x 2
Side_Plates_2

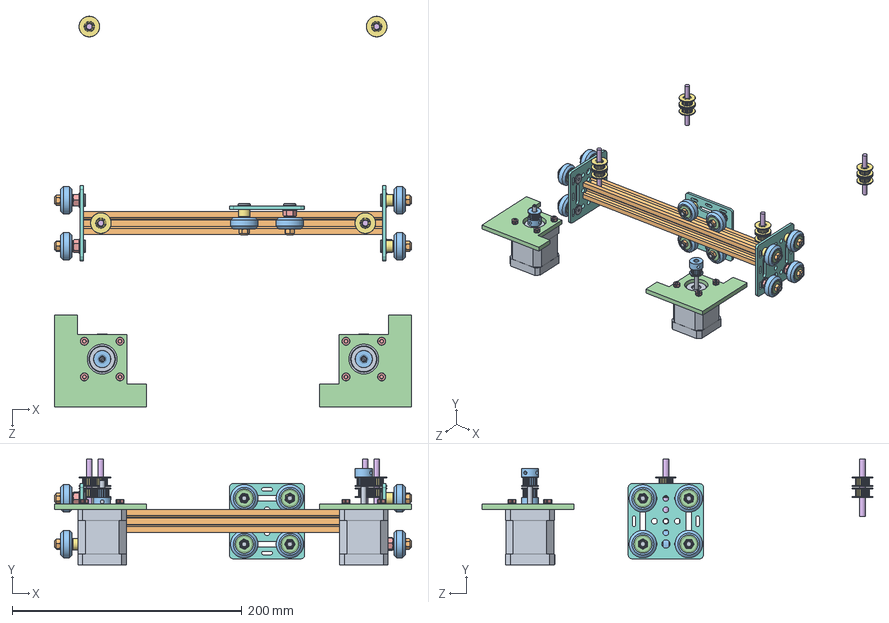
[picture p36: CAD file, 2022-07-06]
CAD Model/XY_Axis_motion.SLDASM
310.6 x 92.0 x 339.8 mm
DC_Steppers x 2
V-slot-aluminum
Solid V-Wheel.stp x 12
Ball Bearing 625 2RS 5x16x5.stp x 24
Eccentric Spacer.stp x 6
1mm 5mm shim.stp x 12
6mm Spacer.stp x 6
20mm gantry plate.stp x 3
M5x25 low profile screw.stp x 12
M5 Nylock.stp x 12
TimingPulley x 2
MotorMount x 2
91290A144_Black-Oxide Alloy Steel Socket Head Screw x 8
pulleyRod x 4
IdlerPulley x 8

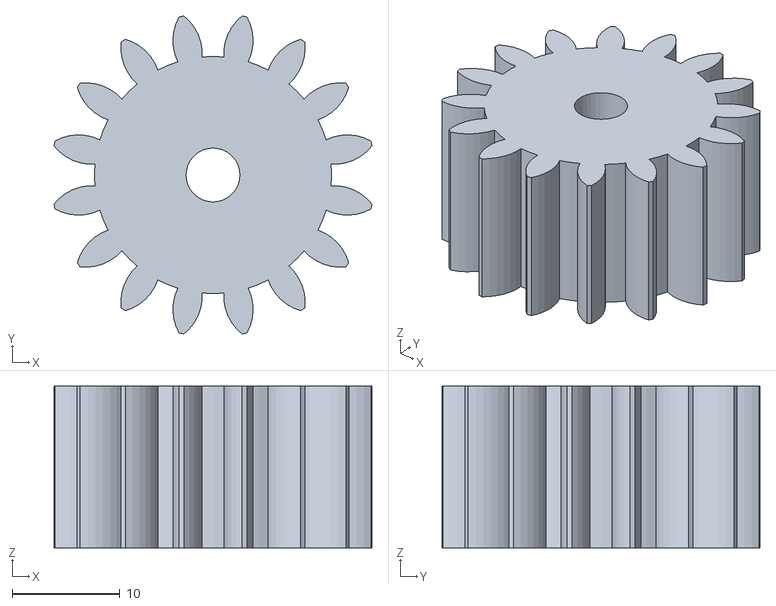
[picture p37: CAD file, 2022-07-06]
CAD Model/3dprint Files/Gear_newgearpump.STL
29.5 x 29.5 x 15.0

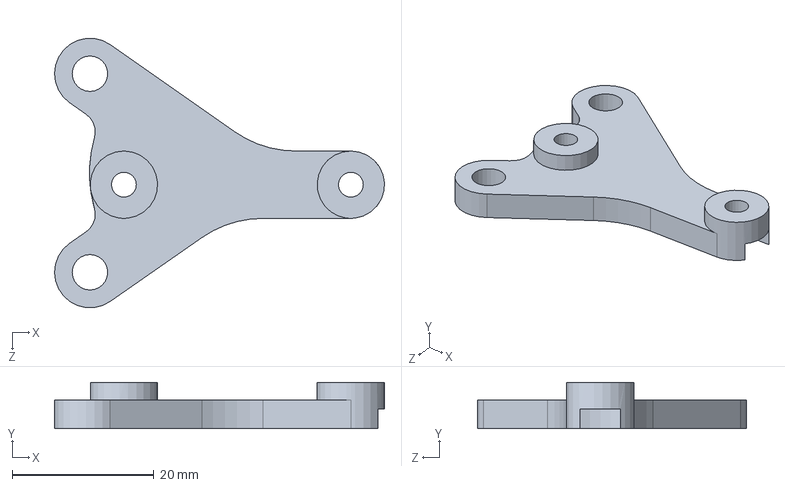
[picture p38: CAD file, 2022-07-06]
CAD Model/fan_mount.SLDPRT
46.5 x 6.50 x 37.9 mm

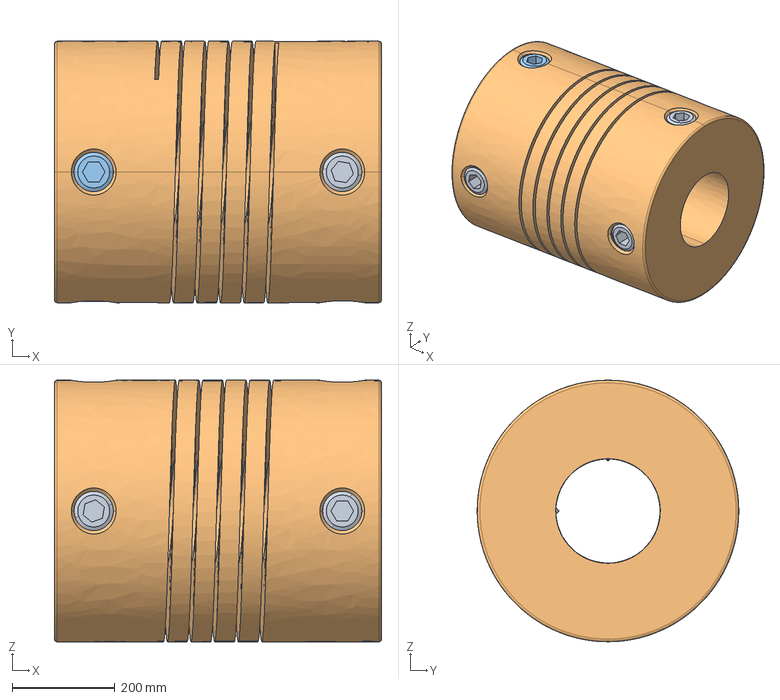
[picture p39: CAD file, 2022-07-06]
CAD Model/flexible-shaft-coupler-8mm-to-8mm-1.snapshot.1/coupling-8x8.stp
635.0 x 508.0 x 508.0 mm

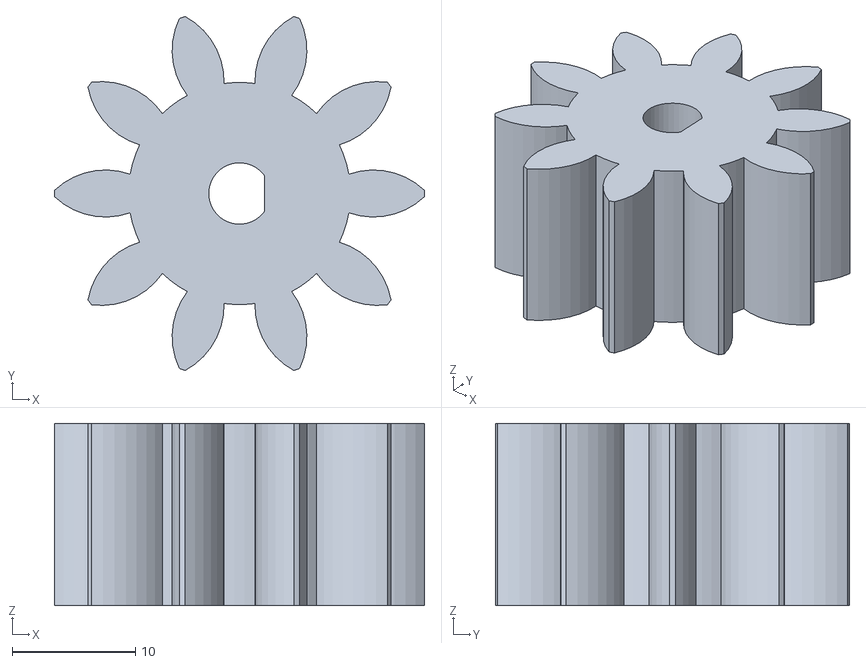
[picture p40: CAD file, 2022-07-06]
CAD Model/New Gear Pump/gear_key_FINAL.STL
30.0 x 28.7 x 14.8

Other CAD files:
CAD Model/3dprint Files/Gear_key_newgearpump.STL
CAD Model/3dprint Files/fan_duct.STL
CAD Model/New Gear Pump/vat_newgearpump.SLDPRT
CAD Model/New Gear Pump/motor_corrector.SLDPRT
CAD Model/2020 3-way corner bracket (v2).SLDPRT
CAD Model/2020 3-way corner bracket.sldprt
CAD Model/20mm Gantry Set.SLDASM
CAD Model/20mm Gantry Set.stp
CAD Model/3-way corner bracket v3 v1.step
CAD Model/3dprint Files/bed_adapter.STL
CAD Model/3dprint Files/fan_mount.STL
CAD Model/3dprint Files/switch mount.STL
CAD Model/5015_Lightweight_Duct_Standard_Left.SLDPRT
CAD Model/5015_Lightweight_Duct_Standard_Left.stl
CAD Model/5015_Lightweight_Duct_Standard_Right.stl
CAD Model/6112K104_Linear Motion Shaft.SLDPRT
CAD Model/61815K34_Base-Mounted Shaft Support.SLDPRT
CAD Model/91290A144_Black-Oxide Alloy Steel Socket Head Screw.SLDPRT
CAD Model/92605A641_Stainless Steel Flat-Tip Set Screw.SLDPRT
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

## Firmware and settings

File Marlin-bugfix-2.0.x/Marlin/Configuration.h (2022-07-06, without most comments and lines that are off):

#pragma once
#define CONFIGURATION_H_VERSION 020008
#define STRING_CONFIG_H_AUTHOR "(thisiskeithb, Ender-3)" // Who made the changes.
#define SHOW_BOOTSCREEN
#define SERIAL_PORT 0
#define BAUDRATE 115200
  #define MOTHERBOARD BOARD_RAMPS_14_EFB
#define CUSTOM_MACHINE_NAME "Choco-3D"
#define EXTRUDERS 1
#define DEFAULT_NOMINAL_FILAMENT_DIA 1.75
#define TEMP_SENSOR_0 1
#define TEMP_SENSOR_1 0
#define TEMP_SENSOR_2 0
#define TEMP_SENSOR_3 0
#define TEMP_SENSOR_4 0
#define TEMP_SENSOR_5 0
#define TEMP_SENSOR_6 0
#define TEMP_SENSOR_7 0
#define TEMP_SENSOR_BED 1
#define TEMP_SENSOR_PROBE 0
#define TEMP_SENSOR_CHAMBER 0
#define DUMMY_THERMISTOR_998_VALUE 25
#define DUMMY_THERMISTOR_999_VALUE 100
#define MAX_REDUNDANT_TEMP_SENSOR_DIFF 10
#define TEMP_RESIDENCY_TIME     10  // (seconds) Time to wait for hotend to "settle" in M109
#define TEMP_WINDOW              1  // (°C) Temperature proximity for the "temperature reached" timer
#define TEMP_HYSTERESIS          3  // (°C) Temperature proximity considered "close enough" to the target
#define TEMP_BED_RESIDENCY_TIME 10  // (seconds) Time to wait for bed to "settle" in M190
#define TEMP_BED_WINDOW          1  // (°C) Temperature proximity for the "temperature reached" timer
#define TEMP_BED_HYSTERESIS      3  // (°C) Temperature proximity considered "close enough" to the target
#define HEATER_0_MINTEMP   5
#define HEATER_1_MINTEMP   5
#define HEATER_2_MINTEMP   5
#define HEATER_3_MINTEMP   5
#define HEATER_4_MINTEMP   5
#define HEATER_5_MINTEMP   5
#define HEATER_6_MINTEMP   5
#define HEATER_7_MINTEMP   5
#define BED_MINTEMP        5
#define HEATER_0_MAXTEMP 275
#define HEATER_1_MAXTEMP 275
#define HEATER_2_MAXTEMP 275
#define HEATER_3_MAXTEMP 275
#define HEATER_4_MAXTEMP 275
#define HEATER_5_MAXTEMP 275
#define HEATER_6_MAXTEMP 275
#define HEATER_7_MAXTEMP 275
#define BED_MAXTEMP      125
#define PIDTEMP
#define BANG_MAX 255     // Limits current to nozzle while in bang-bang mode; 255=full current
#define PID_MAX BANG_MAX // Limits current to nozzle while PID is active (see PID_FUNCTIONAL_RANGE below); 255=full current
#define PID_K1 0.95      // Smoothing factor within any PID loop
    #define DEFAULT_Kp  21.73
    #define DEFAULT_Ki   1.54
    #define DEFAULT_Kd  76.55
#define PIDTEMPBED
#define MAX_BED_POWER 255 // limits duty cycle to bed; 255=full current
  #define DEFAULT_bedKp 57.89
  #define DEFAULT_bedKi 8.62
  #define DEFAULT_bedKd 259.26
  #define PID_FUNCTIONAL_RANGE 10 // If the temperature difference between the target temperature and the actual temperature
#define PREVENT_COLD_EXTRUSION
#define EXTRUDE_MINTEMP 30
#define PREVENT_LENGTHY_EXTRUDE
#define EXTRUDE_MAXLENGTH 600
#define THERMAL_PROTECTION_HOTENDS // Enable thermal protection for all extruders
#define THERMAL_PROTECTION_BED     // Enable thermal protection for the heated bed
#define THERMAL_PROTECTION_CHAMBER // Enable thermal protection for the heated chamber
#define COREYX
#define USE_XMIN_PLUG
#define USE_YMIN_PLUG
#define USE_ZMAX_PLUG
#define X_MIN_ENDSTOP_INVERTING true // Set to true to invert the logic of the endstop.
#define Y_MIN_ENDSTOP_INVERTING true // Set to true to invert the logic of the endstop.
#define Z_MIN_ENDSTOP_INVERTING false // Set to true to invert the logic of the endstop.
#define X_MAX_ENDSTOP_INVERTING false // Set to true to invert the logic of the endstop.
#define Y_MAX_ENDSTOP_INVERTING false // Set to true to invert the logic of the endstop.
#define Z_MAX_ENDSTOP_INVERTING true // Set to true to invert the logic of the endstop.
#define Z_MIN_PROBE_ENDSTOP_INVERTING false // Set to true to invert the logic of the probe.
#define X_DRIVER_TYPE  A4988
#define Y_DRIVER_TYPE  A4988
#define Z_DRIVER_TYPE  A4988
#define E0_DRIVER_TYPE A4988
#define DEFAULT_AXIS_STEPS_PER_UNIT   { 7.5, 7.5, 37.5, 10 }
#define DEFAULT_MAX_FEEDRATE          { 500, 500, 5, 25 }
#define DEFAULT_MAX_ACCELERATION      { 500, 500, 100, 5000 }
#define DEFAULT_ACCELERATION          500    // X, Y, Z and E acceleration for printing moves
#define DEFAULT_RETRACT_ACCELERATION  500    // E acceleration for retracts
#define DEFAULT_TRAVEL_ACCELERATION   500    // X, Y, Z acceleration for travel (non printing) moves
#define DEFAULT_EJERK    5.0  // May be used by Linear Advance
  #define JUNCTION_DEVIATION_MM 0.08  // (mm) Distance from real junction edge
  #define JD_HANDLE_SMALL_SEGMENTS    // Use curvature estimation instead of just the junction angle
#define S_CURVE_ACCELERATION
#define NOZZLE_TO_PROBE_OFFSET { -40, -12, 0 }
#define PROBING_MARGIN 10
#define XY_PROBE_SPEED (133*60)
#define Z_PROBE_SPEED_FAST (4*60)
#define Z_PROBE_SPEED_SLOW (Z_PROBE_SPEED_FAST / 2)
#define Z_CLEARANCE_DEPLOY_PROBE   10 // Z Clearance for Deploy/Stow
#define Z_CLEARANCE_BETWEEN_PROBES  5 // Z Clearance between probe points
#define Z_CLEARANCE_MULTI_PROBE     5 // Z Clearance between multiple probes
#define Z_PROBE_LOW_POINT          -2 // Farthest distance below the trigger-point to go before stopping
#define Z_PROBE_OFFSET_RANGE_MIN -20
#define Z_PROBE_OFFSET_RANGE_MAX 20
#define X_ENABLE_ON 0
#define Y_ENABLE_ON 0
#define Z_ENABLE_ON 0
#define E_ENABLE_ON 0 // For all extruders
#define DISABLE_X false
#define DISABLE_Y false
#define DISABLE_Z false
#define DISABLE_E false             // Disable the extruder when not stepping
#define DISABLE_INACTIVE_EXTRUDER   // Keep only the active extruder enabled
#define INVERT_X_DIR true
#define INVERT_Y_DIR false
#define INVERT_Z_DIR false
#define INVERT_E0_DIR true
#define INVERT_E1_DIR false
#define INVERT_E2_DIR false
#define INVERT_E3_DIR false
#define INVERT_E4_DIR false
#define INVERT_E5_DIR false
#define INVERT_E6_DIR false
#define INVERT_E7_DIR false
#define X_HOME_DIR -1
#define Y_HOME_DIR -1
#define Z_HOME_DIR 1
#define X_BED_SIZE 115
#define Y_BED_SIZE 120
#define X_MIN_POS 0
#define Y_MIN_POS 0
#define Z_MIN_POS 0
#define X_MAX_POS X_BED_SIZE
#define Y_MAX_POS Y_BED_SIZE
#define Z_MAX_POS 204
#define MIN_SOFTWARE_ENDSTOPS
  #define MIN_SOFTWARE_ENDSTOP_X
  #define MIN_SOFTWARE_ENDSTOP_Y
  #define MIN_SOFTWARE_ENDSTOP_Z
#define MAX_SOFTWARE_ENDSTOPS
  #define MAX_SOFTWARE_ENDSTOP_X
  #define MAX_SOFTWARE_ENDSTOP_Y
  #define MAX_SOFTWARE_ENDSTOP_Z
#define LEVEL_BED_CORNERS
  #define LEVEL_CORNERS_INSET_LFRB { 30, 30, 30, 30 } // (mm) Left, Front, Right, Back insets
  #define LEVEL_CORNERS_HEIGHT      0.0   // (mm) Z height of nozzle at leveling points
  #define LEVEL_CORNERS_Z_HOP       4.0   // (mm) Z height of nozzle between leveling points
#define HOMING_FEEDRATE_MM_M { (20*60), (20*60), (4*60) }
#define VALIDATE_HOMING_ENDSTOPS
#define EEPROM_SETTINGS       // Persistent storage with M500 and M501
#define EEPROM_CHITCHAT       // Give feedback on EEPROM commands. Disable to save PROGMEM.
#define EEPROM_BOOT_SILENT    // Keep M503 quiet and only give errors during first load
  #define EEPROM_AUTO_INIT  // Init EEPROM automatically on any errors.
#define HOST_KEEPALIVE_FEATURE        // Disable this if your host doesn't like keepalive messages
#define DEFAULT_KEEPALIVE_INTERVAL 2  // Number of seconds between "busy" messages. Set with M113.
#define BUSY_WHILE_HEATING            // Some hosts require "busy" messages even during heating
#define PREHEAT_1_LABEL       "Choco"
#define PREHEAT_1_TEMP_HOTEND 45
#define PREHEAT_1_TEMP_BED    45
#define PREHEAT_1_FAN_SPEED   255 // Value from 0 to 255
#define NOZZLE_PARK_FEATURE
  #define NOZZLE_PARK_POINT { (X_MIN_POS + 10), (Y_MAX_POS - 10), 20 }
  #define NOZZLE_PARK_Z_RAISE_MIN   2   // (mm) Always raise Z by at least this distance
  #define NOZZLE_PARK_XY_FEEDRATE 100   // (mm/s) X and Y axes feedrate (also used for delta Z axis)
  #define NOZZLE_PARK_Z_FEEDRATE    5   // (mm/s) Z axis feedrate (not used for delta printers)
#define PRINTJOB_TIMER_AUTOSTART
#define LCD_LANGUAGE en
#define DISPLAY_CHARSET_HD44780 JAPANESE
#define LCD_INFO_SCREEN_STYLE 0
#define SDSUPPORT
#define REVERSE_ENCODER_DIRECTION
#define INDIVIDUAL_AXIS_HOMING_MENU
#define REPRAP_DISCOUNT_SMART_CONTROLLER
#define SOFT_PWM_SCALE 0
#define SERVO_DELAY { 300 }

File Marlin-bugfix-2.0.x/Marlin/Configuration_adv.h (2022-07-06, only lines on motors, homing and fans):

#define E0_AUTO_FAN_PIN -1
#define E1_AUTO_FAN_PIN -1
#define E2_AUTO_FAN_PIN -1
#define E3_AUTO_FAN_PIN -1
#define E4_AUTO_FAN_PIN -1
#define E5_AUTO_FAN_PIN -1
#define E6_AUTO_FAN_PIN -1
#define E7_AUTO_FAN_PIN -1
#define CHAMBER_AUTO_FAN_PIN -1
#define HOMING_BUMP_MM      { 0, 0, 2 }       // (mm) Backoff from endstops after first bump
#define HOMING_BUMP_DIVISOR { 2, 2, 4 }       // Re-Bump Speed Divisor (Divides the Homing Feedrate)
#define QUICK_HOME                            // If G28 contains XY do a diagonal move first
#define MICROSTEP_MODES { 16, 16, 16, 16, 16, 16 } // [1,2,4,8,16]
#define LIN_ADVANCE
  #define LIN_ADVANCE_K 0.0    // Unit: mm compression per 1mm/s extruder speed
#define ADVANCED_PAUSE_FEATURE
  #define ADVANCED_PAUSE_PURGE_FEEDRATE        3  // (mm/s) Extrude feedrate (after loading). Should be slower than load feedrate.
  #define ADVANCED_PAUSE_PURGE_LENGTH         50  // (mm) Length to extrude after loading.
  #define ADVANCED_PAUSE_RESUME_PRIME          0  // (mm) Extra distance to prime nozzle after returning from park.
  #define HOME_BEFORE_FILAMENT_CHANGE           // If needed, home before parking for filament change

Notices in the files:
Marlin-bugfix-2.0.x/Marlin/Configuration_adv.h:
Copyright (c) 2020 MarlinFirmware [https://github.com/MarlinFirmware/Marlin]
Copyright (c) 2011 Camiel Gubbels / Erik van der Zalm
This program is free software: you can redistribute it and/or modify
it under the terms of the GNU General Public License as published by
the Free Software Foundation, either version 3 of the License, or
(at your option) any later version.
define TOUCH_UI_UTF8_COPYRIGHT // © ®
